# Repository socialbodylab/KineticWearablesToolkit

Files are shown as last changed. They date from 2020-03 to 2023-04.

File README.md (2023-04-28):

# Kinetic Wearables Toolkit

## Table of contents
* [General info](#general-info)
* [In Use](#in-use)
* [Servo 90 Degree](#servo-90-degree)
* [Servo Flex Base](#servo-flex-base)
* [Servo Linear Adaptor](#servo-linear-adaptor)
* [Micro Stepper Motor](#micro-stepper-motor)
* [Solenoid](#solenoid)
* [BOM](#bill-of-materials)
* [Status](#status)
* [License](#license)
* [Contact](#contact)

## General info
These designs make up a wearable electronics toolkit for electronically animating clothing and accessories using several types of small electric motors for fashion, design and DIY electronics. The toolkit offers several kinds of motion in multiple axes using 3D printed parts and lightweight, inexpensive motor/actuators with multiple attachment options. This toolkit represents the result of our initial work in this area, and provides a basis for building wearable prototypes, finished designs, and for developing further design considerations through experimentation and testing.

## In Use

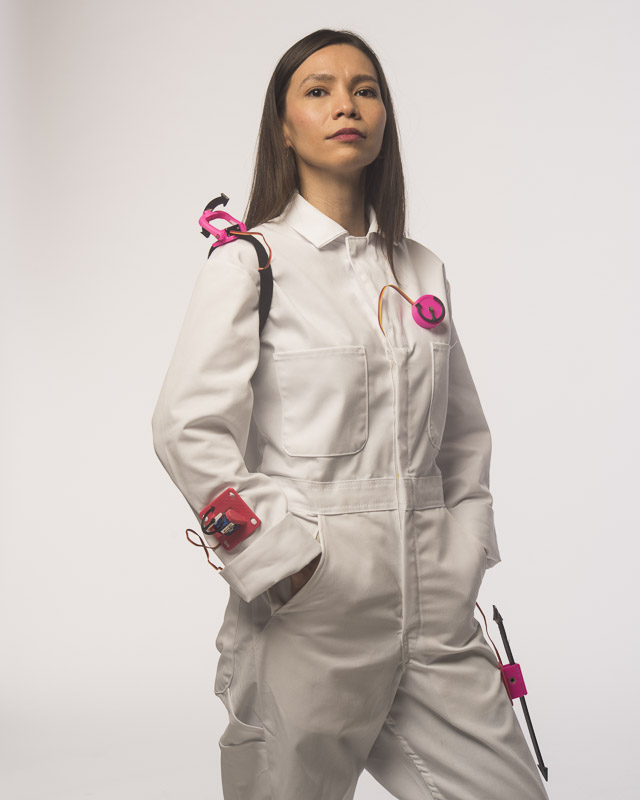
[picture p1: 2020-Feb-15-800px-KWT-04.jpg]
Example image


Above: Some elements of the toolkit. Black arrows illustrate direction of movement.

## Servo 90 Degree

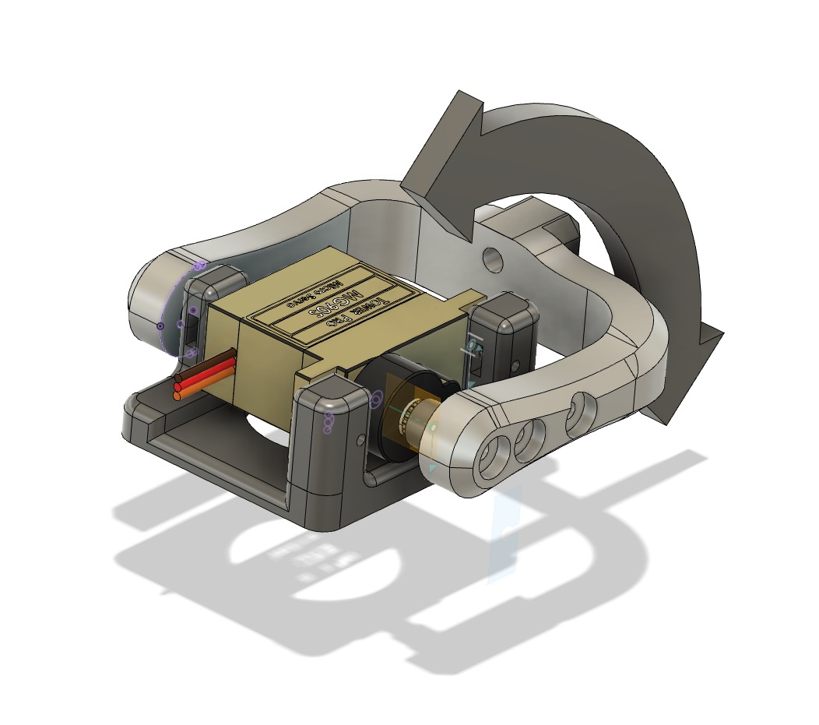
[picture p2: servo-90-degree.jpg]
Servo 90 Degree


* Using a common 9g micro servo motor
* Pivots in base add support for higher loads
* 3D printable in PLA or other rigid material. We use polycarbonate.
* Attaches with pin/slot or strap

## Servo Flex Base

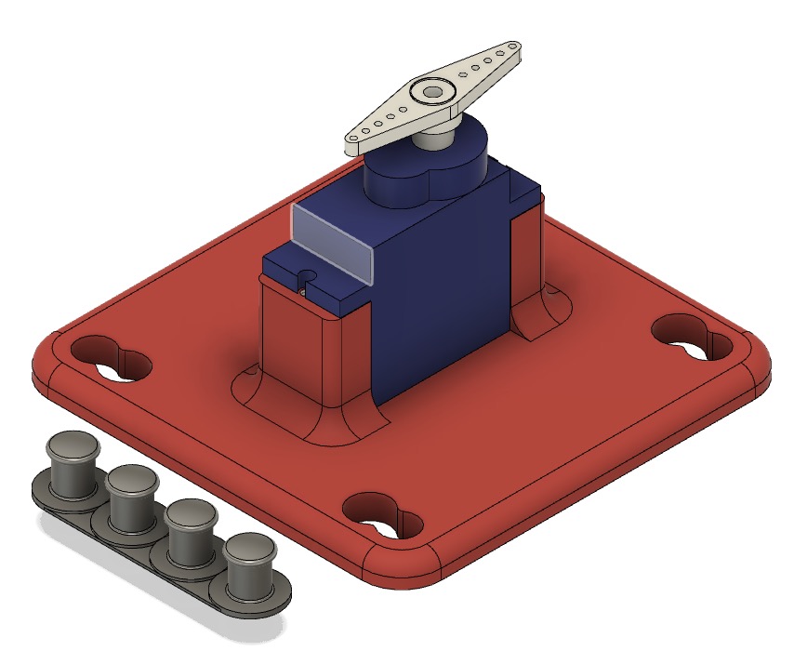
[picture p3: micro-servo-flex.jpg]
Servo Flex Base


* 9g micro servo motor is attached using M2 bolts
* 3D printable in TPU or other flexible material. We use Ninjaflex.
* Attaches with pin/slot in a fixed position or can be mounted with a strap

## Servo Flex Tilt Base

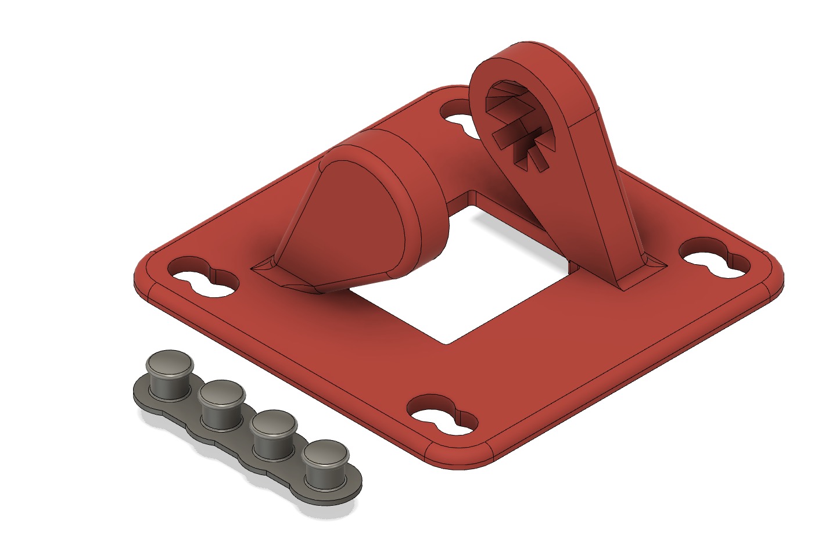
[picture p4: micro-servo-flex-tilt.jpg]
Servo Flex Tilt Base


* 9g micro servo motor can be installed in multiple orientations, without tools
* 3D printable in TPU or other flexible material. We use Ninjaflex.
* Attaches with pin/slot in a fixed position or can be rotated under a strap.

## Servo Linear Adaptor

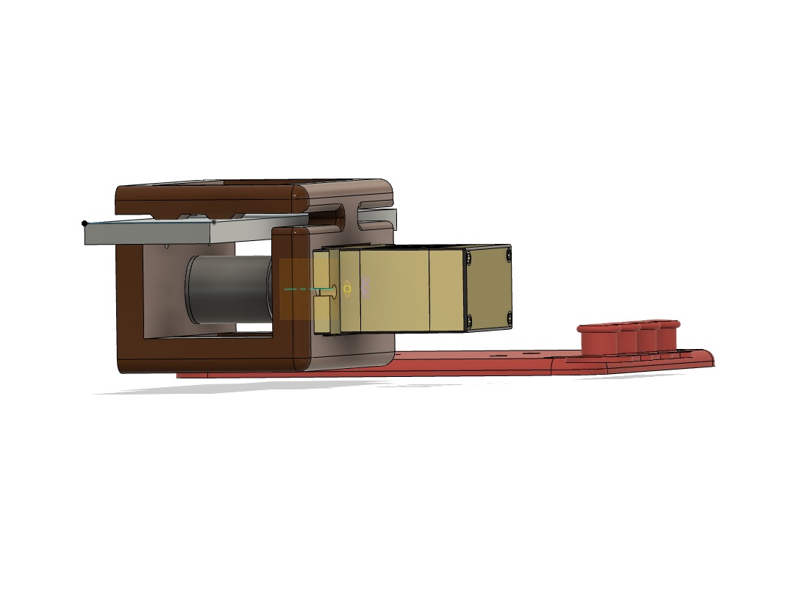
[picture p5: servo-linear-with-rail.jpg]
Example Image


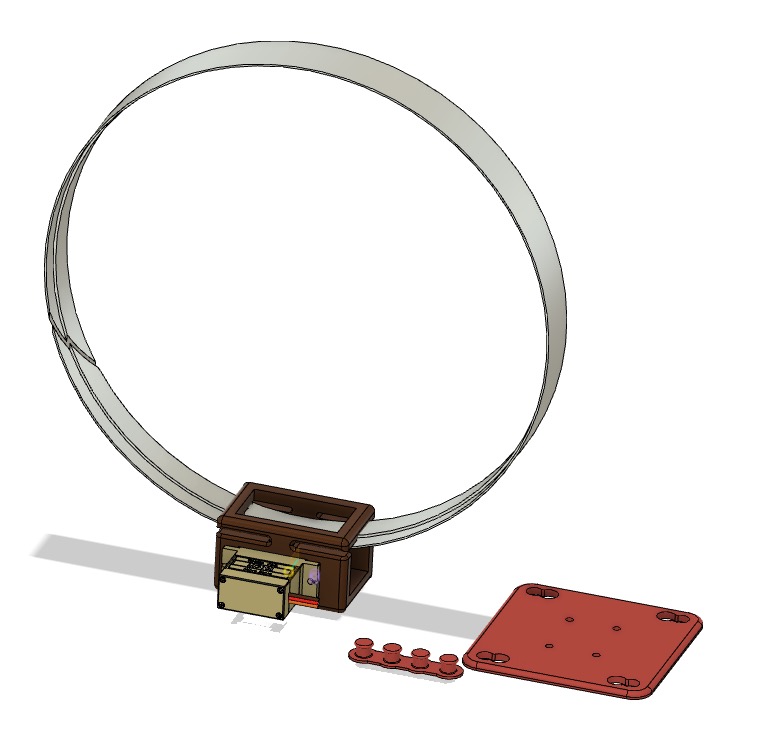
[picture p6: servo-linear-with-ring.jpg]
Linear adaptor with ring


* 9g micro servo motor drives a wheel which drives a rail of any length.
* Rail can be curved as shown in first image above
* Rail can be straight as shown in second image above
* Flexible tire is not included in the CAD model above. We used a rubber grommet.
* As with Servo Flex Base above, servo can be 180 degree or continuous type motor.
* Linear adaptor is 3D printable in PLA or other rigid material.
* Linear adaptor bolts to flexible base in one of two orientations.
* Base uses pin/slot to attach to fabric.

## Micro Stepper Motor

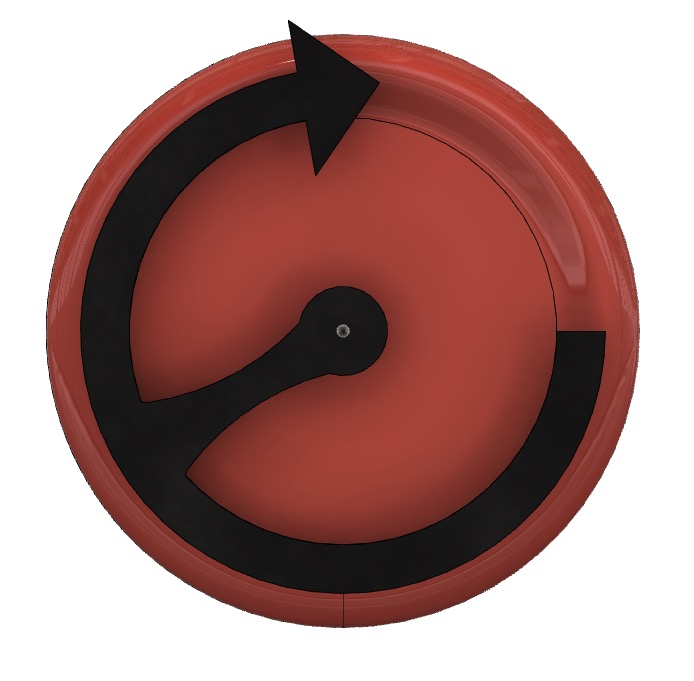
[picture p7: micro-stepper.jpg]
Micro stepper motor


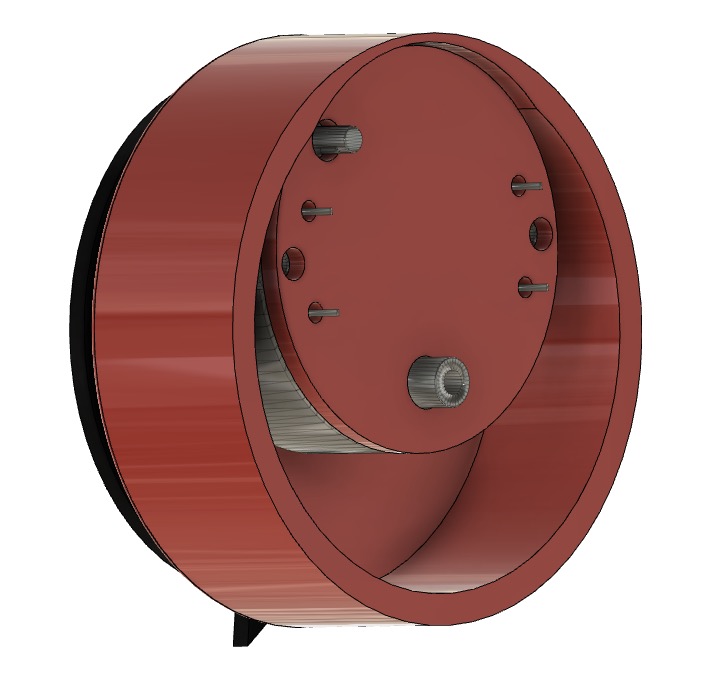
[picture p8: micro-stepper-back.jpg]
Micro stepper motor back


* Uses small x27.168 stepper motor (Switec X 27 series)
* Attaches to cloth using lapel pin (not shown)
* 3D printable in PLA or other rigid material
* Suitable for moving very light loads only

## Solenoid

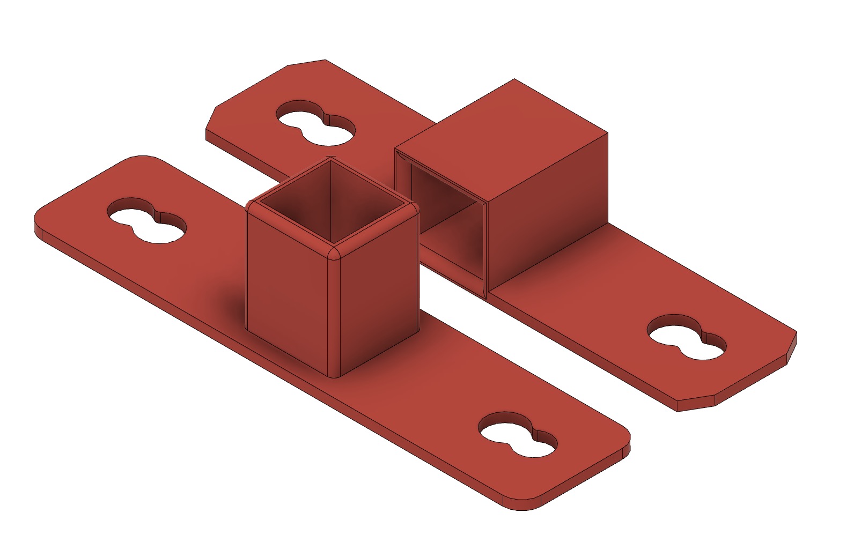
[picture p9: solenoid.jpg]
Solenoid


* Uses small 5V solenoid (e.g. https://www.digikey.ca/product-detail/en/sparkfun-electronics/ROB-11015/1568-1592-ND/6163694)
* Soloid is press fit in either mount, flat or 90 degree.
* Mount is 3D printable in TPU or other flexible material.
* We recommend 3D printing (FDM) with square aperture of each part facing up to avoid the need for support structures.
* Be mindful of heat buildup if solenoid is energized at a high duty cycle.

## Bill of Materials
This bill of materials is shown in the photo "Complete Toolkit.jpg". The stepper motor can be made to work without the stepper motor driver featherwing shown.

|  **Fabricated parts:** |  |  |  |  |
| --- | --- | --- | --- | --- |
|  Part/Assembly | Qty | Material |  |  |
|  Micro servo flex base | 1 | TPU/Ninjaflex |  |  |
|  Micro servo flex tilt base | 1 | TPU/Ninjaflex |  |  |
|  micro stepper rotobrooch | 1 | PLA |  |  |
|  Servo 90 deg base | 1 | TPU/Ninjaflex |  |  |
|  Solenoid v3 (both parts) | 1 | TPU/Ninjaflex |  |  |
|  Servo linear adaptor | 1 | TPU/Ninjaflex and PLA |  |  |
|  Servo linear rail (various sizes available) | 1 | PLA |  |  |
| |  |  |  |  |
| |  |  |  |  |
|  **Purchased parts:** |  |  |  |  |
| |  |  |  |  |
|  Part | Qty | Price/ea | Supplier | Link |
| Gauge stepper motor | 1 | $4.99/ea  | Tanin Auto Electronix | https://www.taninautoelectronix.com/product/x27-168-switec-juken-gm-gmc-chevrolet-stepper-motor/ |
| | 1 | $19.99 with optional breakout board | Tindie | https://www.tindie.com/products/TheRengineer/analog-gauge-stepper-breakout-board |
|  Pull solenoid 5V | 1 | $5.50 | Digikey/Sparkfun | https://www.digikey.com/en/products/detail/sparkfun-electronics/ROB-11015/6163694 |
|  180 degree servo | 1 | $5.00 | Digikey/DF Robotics | https://www.digikey.com/en/products/detail/dfrobot/SER0049/13280116  |
|  Full rotation servo | 1 | $7.50 | Digikey/Adafruit Industries | https://www.digikey.com/en/products/detail/adafruit-industries-llc/2442/5774227 |
|  M2x0.4 bolt x 10mm (SHCS or BHCS) | 10 | $0.08/ea | Fastenal | https://www.fastenal.com/product/details/0134599 |
|  3/8"ID x 5/8"OD Black Rubber Grommet |  | $0.52/ea | Fastenal | https://www.fastenal.com/product/details/11120335 |
| |  |  |  |  |
| |  |  |  |  |
|  **Not included (but may be needed for full build)** |  |  |  |  |
|  LiPoly battery |  |  |  |  |
|  Arduino microcontroller |  |  |  |  |
|  Hookup wire |  |  |  |  |
|  Velcro® Brand Self-Grip Straps - 3⁄4" x 75' |  | $37/75 feet | Uline | https://www.uline.com/Product/ProductDetailRootItem?modelnumber=S-8136 |

## Status
Project is: _released_

## License
Creative Commons Attribution-NonCommercial-ShareAlike (CC BY-NC-SA)

## Contact
Created by [@socialbodylab](https://www.socialbodylab.com) - feel free to contact us!

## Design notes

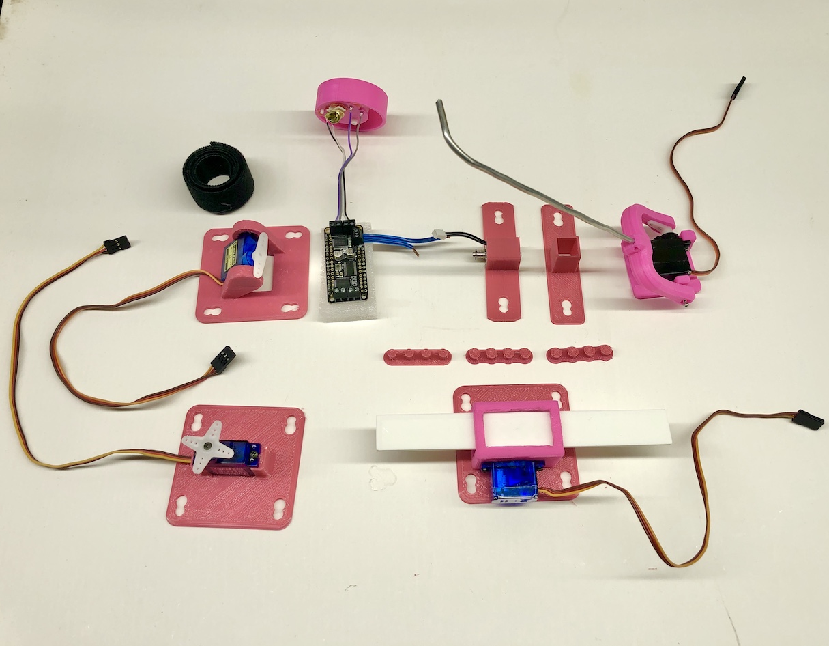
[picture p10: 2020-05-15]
Complete Toolkit.jpg

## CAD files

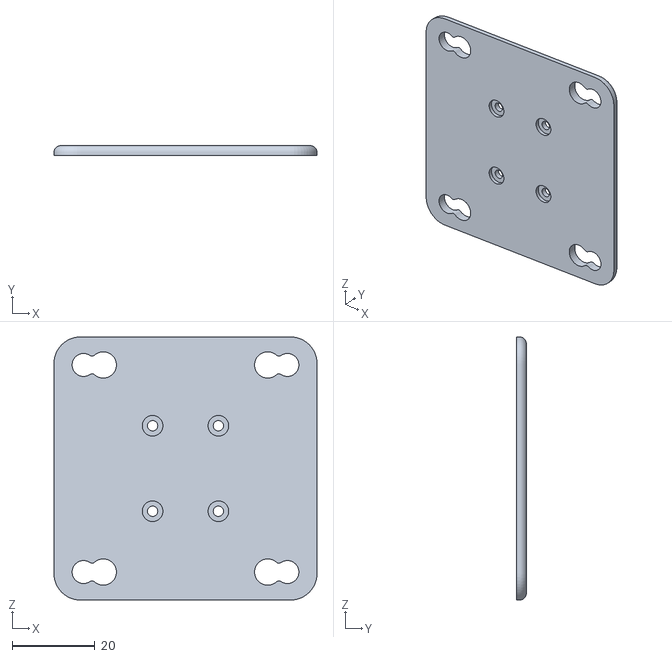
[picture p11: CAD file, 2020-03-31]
servo linear adapter flex base.stl
63.5 x 2.38 x 63.5

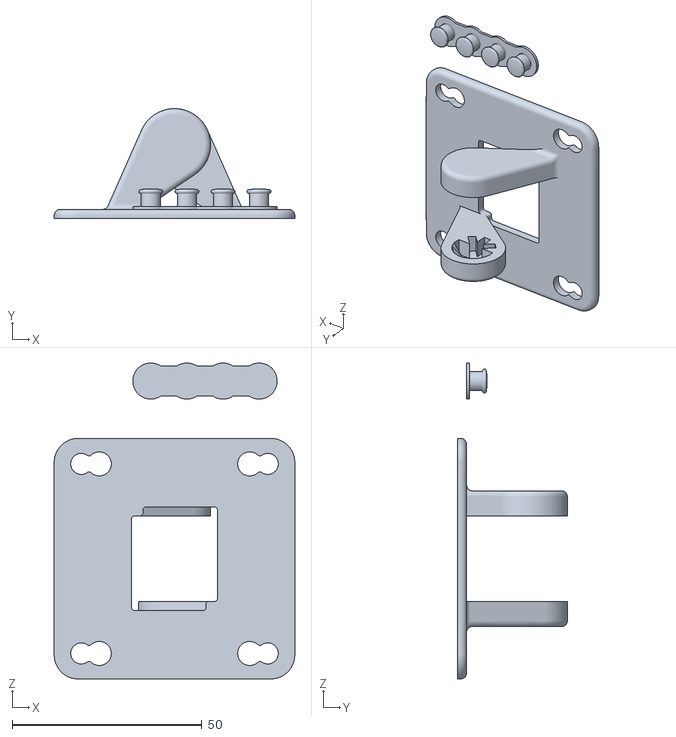
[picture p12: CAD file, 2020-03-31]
Micro servo flex tilt base v4.stl
63.5 x 29.0 x 83.4

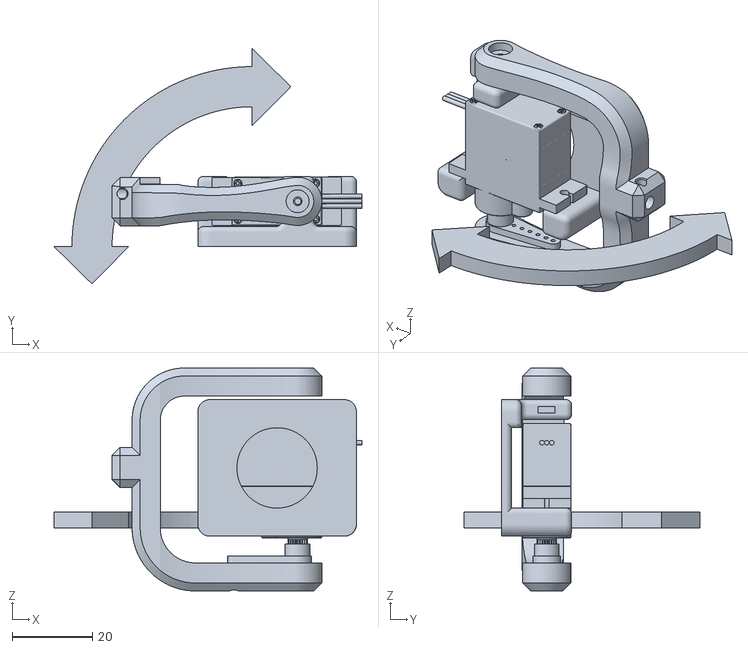
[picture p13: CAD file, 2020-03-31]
Servo 90deg v2.stl
76.7 x 58.7 x 55.5

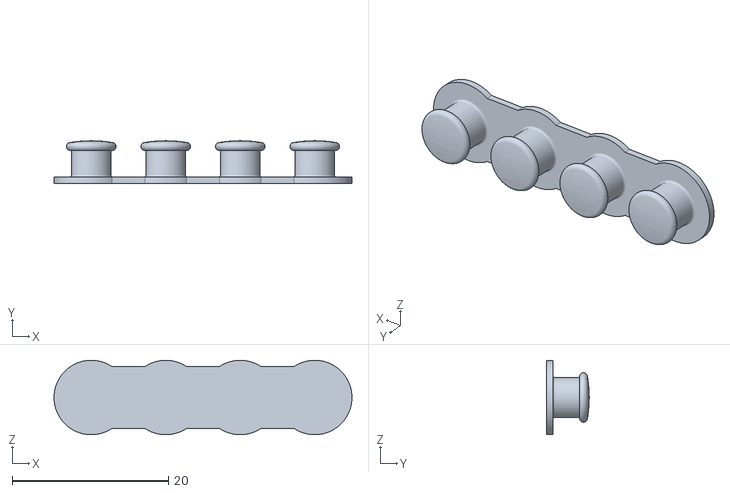
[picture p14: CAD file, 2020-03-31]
servo linear adapter flex base pin.stl
38.1 x 5.44 x 9.52

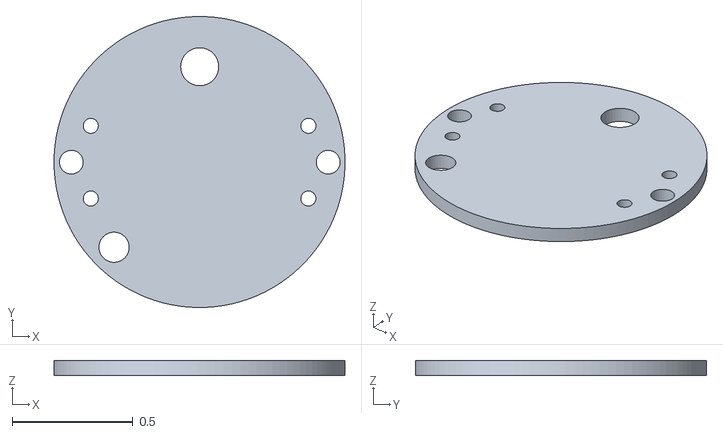
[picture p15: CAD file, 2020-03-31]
micro stepper rotobrooch backing.stl
1.20 x 1.20 x 0.0625

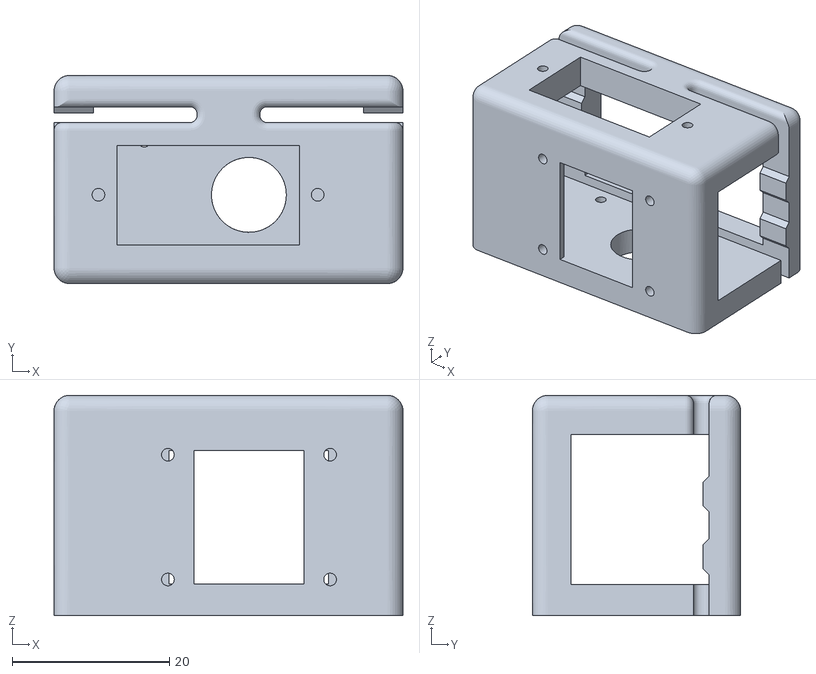
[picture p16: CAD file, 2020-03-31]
Servo linear adapter base.stl
44.4 x 26.5 x 28.0

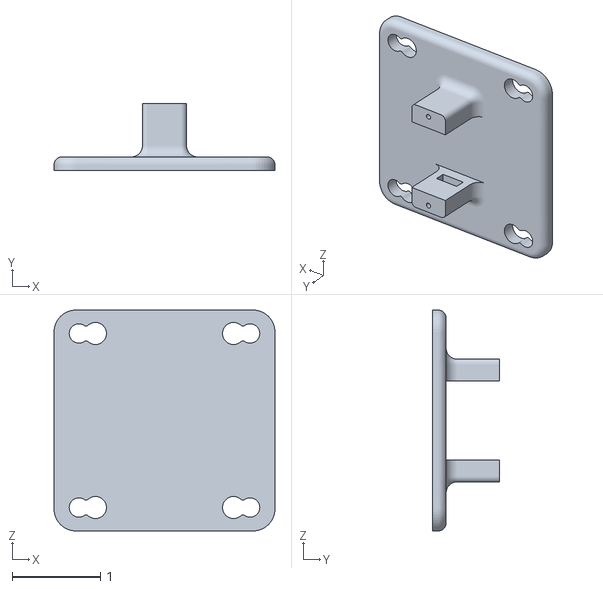
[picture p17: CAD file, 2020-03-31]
micro servo flex base.stl
2.50 x 0.762 x 2.50

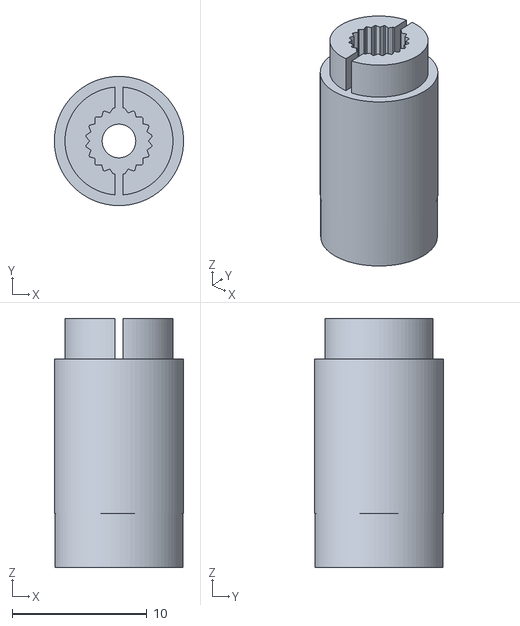
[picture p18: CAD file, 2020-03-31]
servo linear adapter drive wheel.stl
9.60 x 9.60 x 18.5

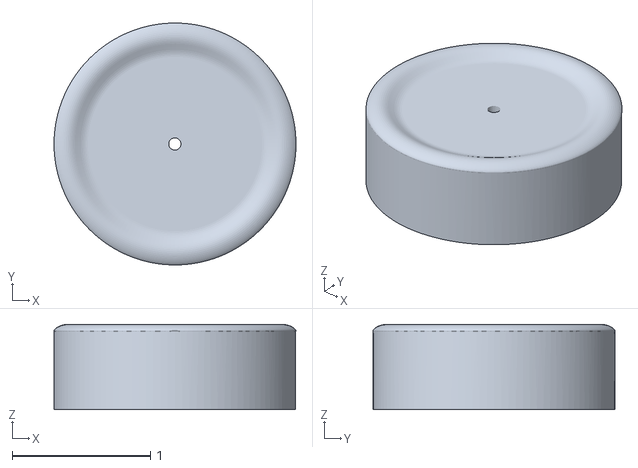
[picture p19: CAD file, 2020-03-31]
micro stepper rotobrooch.stl
1.75 x 1.75 x 0.616

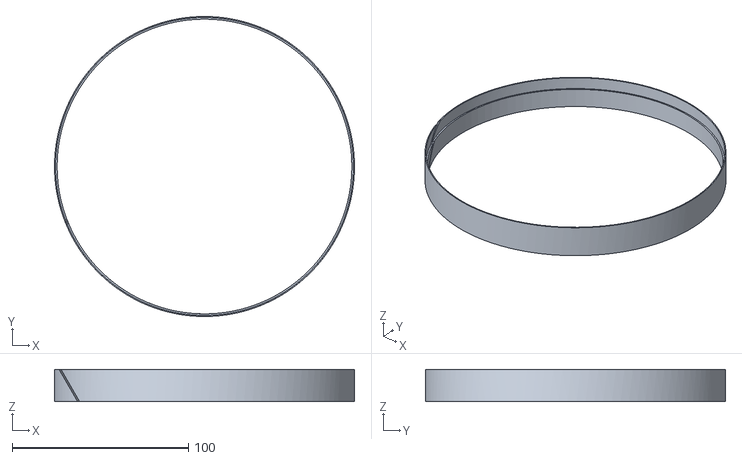
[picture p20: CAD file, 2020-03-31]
Servo linear adapter ring.stl
170.0 x 170.0 x 18.2

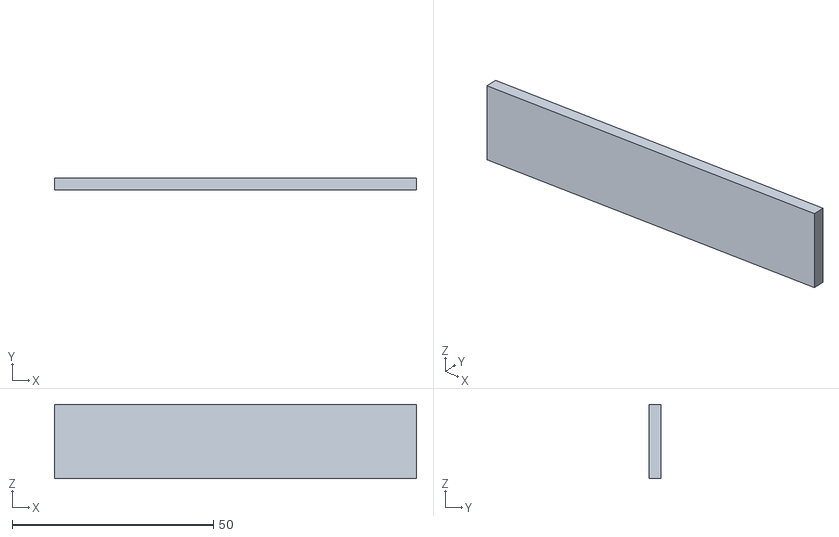
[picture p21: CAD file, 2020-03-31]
Servo linear adapter rail.stl
90.0 x 3.00 x 18.5

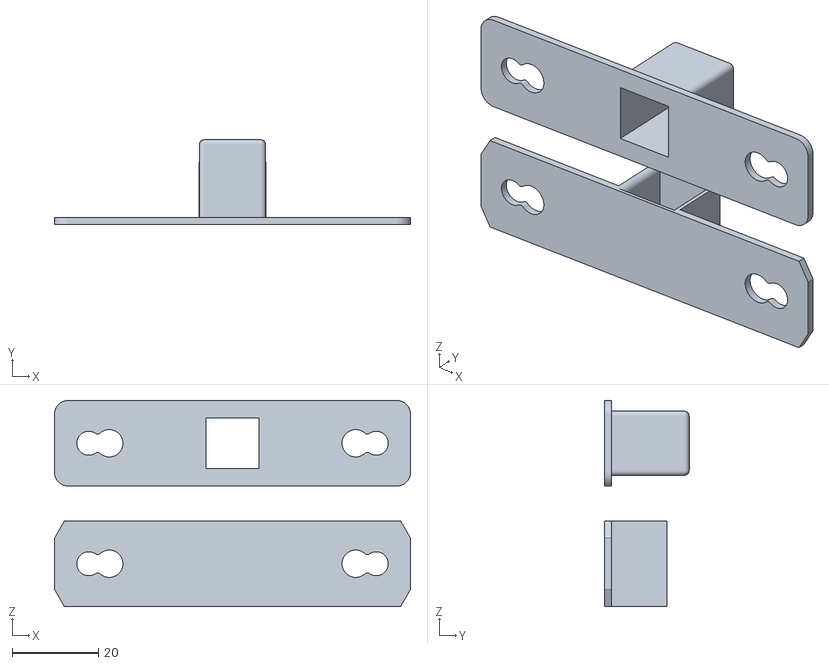
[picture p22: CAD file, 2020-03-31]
Solenoid v3.stl
82.6 x 19.6 x 47.8

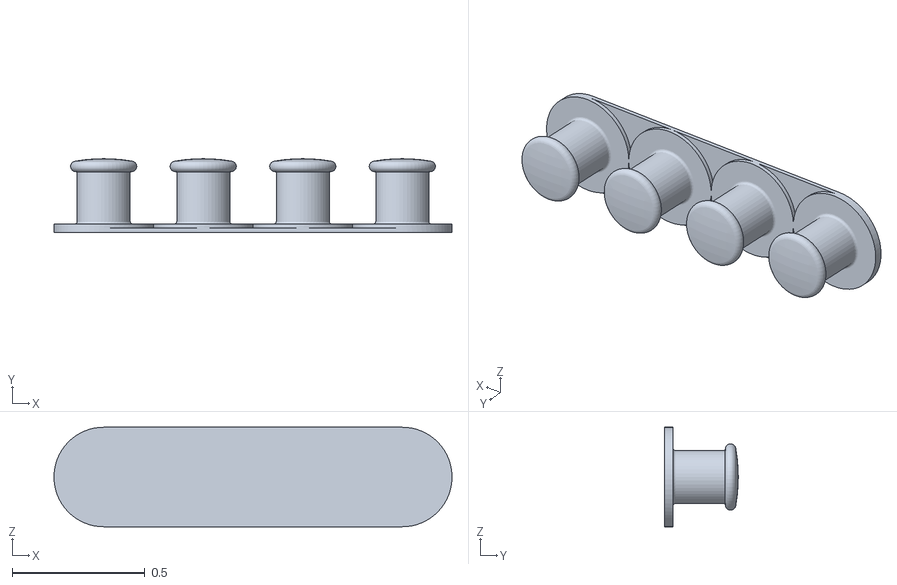
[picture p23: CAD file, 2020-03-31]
micro servo flex base pin.stl
1.50 x 0.277 x 0.375

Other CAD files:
Micro servo flex base v5.f3z
Micro servo flex tilt base v4.f3z
Micro stepper rotobrooch v5.f3d
Solenoid v3.f3d

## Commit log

2020-03-31 Initial commit
    This is the Kinetic Wearables Toolkit as presented in our submission to DIS 2020, representing the first generation of the toolkit
    [Micro servo flex base v5.f3z, Micro servo flex tilt base v4.f3z, Micro servo flex tilt base v4.stl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]
2020-05-15 Added BOM
2023-04-28 Update BOM with current US vendors and prices
